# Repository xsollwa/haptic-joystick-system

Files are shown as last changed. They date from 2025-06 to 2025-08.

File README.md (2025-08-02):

# haptic-joystick-system
A handheld controller that uses air pressure to send haptic feedback.

**Created by:** Ruzanna Gaboyan and Philip Golczak

**Date:** June 7, 2025

## Overview

The **Haptic Joystick System** is a *wireless controller that lets you wirelessly control robot arms in XYR directions* using your hand movement and pressure. It includes a two dual axis joystick modules for motion control in XYR directions, and a small squeezable air bulb that sends and receives air pressure signals. The controller *reads how hard you're squeezing using an air pressure sensor and can also send pressure back* into the bulb to communicate resistance.

**Why we made it**: By this project we wanted to make controlling robots more natural by *"feeling what they feel"* in addition to just moving them. This is useful especially in robotics tasks where pressure precision applied by the robot matters: like gripping and squeezing fragile objects. 

//////Note: we removed the screen feature to bring the cost of the project down.

## Features
- **Pneumatic haptic feedback system:** Squeeze a small air bulb to send signals to a robot arm.
- **Joystick control**: Move the robot arm in XYR *(R-Rotation)* directions.
- **Two-way haptic feedback communication:** Air pumping piston mechanism also sends pressure back into the bulb when robot grips something.
- **Wireless communication:** ESP32 hamdles communication between the controller and the robot over Wi-Fi.
- **Custom PCB and 3D case:** Designed and built from scratch for this project.
- **OLED Display:** A little screen shows live data like grip pressure, feedback intensity and other info.
- **Ergonomic handle options:** In addition to the default casing, we CAD-ed an alternate ergonomic grip design for more comfort that can be added on the controller.

Ergonomic handle options: In addition to the default casing, we CAD-modeled an alternate ergonomic grip design for added comfort and modularity when holding the controller.

### Materials and Budget

## Bill of Materials

| Part Number | Part Name | Description | Unit Price | Total Price | Link |
|---|---|---|---|---|---|
| MP1 | ESP32 | Wi-Fi Microprocessor | $5.99 | $5.99 | [Amazon](https://www.amazon.com/gp/product/B0DDPJQX3X/ref=ox_sc_act_image_11?smid=A1VTL661FOEJB1&th=1) |
| J1, J2 | Joystick Module (2x)| KY-023 control joystick module | $6.79 | $6.79 | [Amazon](https://www.amazon.com/Joystick-Sensor-Module-Controller-KY-023/dp/B08681KFSD/) |
| S1 | AITRIP Pressure Sensor | Barometric Pressure Sensor Module | $9.99 | $9.99 | [Amazon](https://www.amazon.com/AITRIP-Pressure-Digital-Barometric-Controller/dp/B09KXXBCYX/) |
| PCB1 | PCB | Fabricated PCB | $5.00 | $5.00 | [PCBWay](https://pcbway.com/) |
| BT1 | Battery Connector | Plug in for LiPo battery | $3.77 | $3.77 | [Amazon](https://www.amazon.com/gp/product/B0DY5GRSQW/ref=ox_sc_act_title_7?smid=AH55IWDCGXER3&psc=1) |
| BULB | Pipet bulb | 4ml Air bulb for pressure sensor | $7.98 | $7.98 | [Amazon](https://www.amazon.com/gp/product/B01LZHMLQA/ref=ox_sc_act_title_6?smid=A29JIFH4ZXPNL8&psc=1) |
| TUBE | Tubes | Tube to connect the sensor, pump and air bulb | $7.49 | $7.49 | [Amazon](https://www.amazon.com/uxcell-Silicone-Tubing-Rubber-Transfer/dp/B085N17TDB/) |
| CN1 | Tube T-Connectors | Connectors for the tube, air bulb, sensor, pump | $11.99 | $11.99 | [Amazon](https://www.amazon.com/gp/product/B06XGCM2RX/ref=ox_sc_act_title_5?smid=A1THAZDOWP300U&psc=1) |
| SYRINGE | Syringe | 10ml Syringe for inflating and deflating | $5.99 | $5.99 | [Amazon](https://www.amazon.com/Plastic-Syringe-Measurement-Scientific-Measuring/dp/B09MYPTD1P/) |
| AT1 | Actuator | Mini Linear Actuator to push air | $19.99 | $19.99 | [Amazon](https://www.amazon.com/Actuator-Electric-Actuators-Robotics-Automation/dp/B0D17H1HGV/) |
| MD1 | Motor Driver | Stepper Motor Driver Module | $6.98 | $6.98 | [Amazon](https://www.amazon.com/WWZMDiB-L298N-H-Bridge-Controller-Raspberry/dp/B0CR6BX5QL/) |
| **TOT** | **Total (excl. taxes & shipping)** | | | **$91.96**  | |
| | **Total WITH taxes & shipping** | | | **$114.50** | |

## Notes on Purchasing and Shipping

We want to purchase most of the parts from Amazon. We chose Amazon as our primary supplier because we have access to Amazon Prime, which has faster shipping. The prime shipping makes the packs cheaper than the singular alternatives at other sources (like AliExpress). Also, we own some of the parts, like the battery and boost converter, so their cost is put as $0. 

//Note: The difference between Aliexpress sourcing and Amazon sourcing for this project is ~$7.00

## How it Works
1) Joystick modules send movement data wirelessly through ESP32 to the robot arm,
2) When you squeeze the air bulb the pressure sensor reads the force,
3) ESP32 sends that signal to the robot (like our [Remote Assist Hand](https://github.com/xsollwa/remote-assist-hand), but the controller can potentially be used on other robots as well),
4) If the robot grips something, it sends resistance signals back,
5) Air pumping mechanism activates and sends pressure into the bulb,
6) You feel it!
7) OLED screen displays pressure data, joystick values, connection status and more. Pressing either joystick down switched between display modes.

## Pictures 
**PCB**

<p align="center">
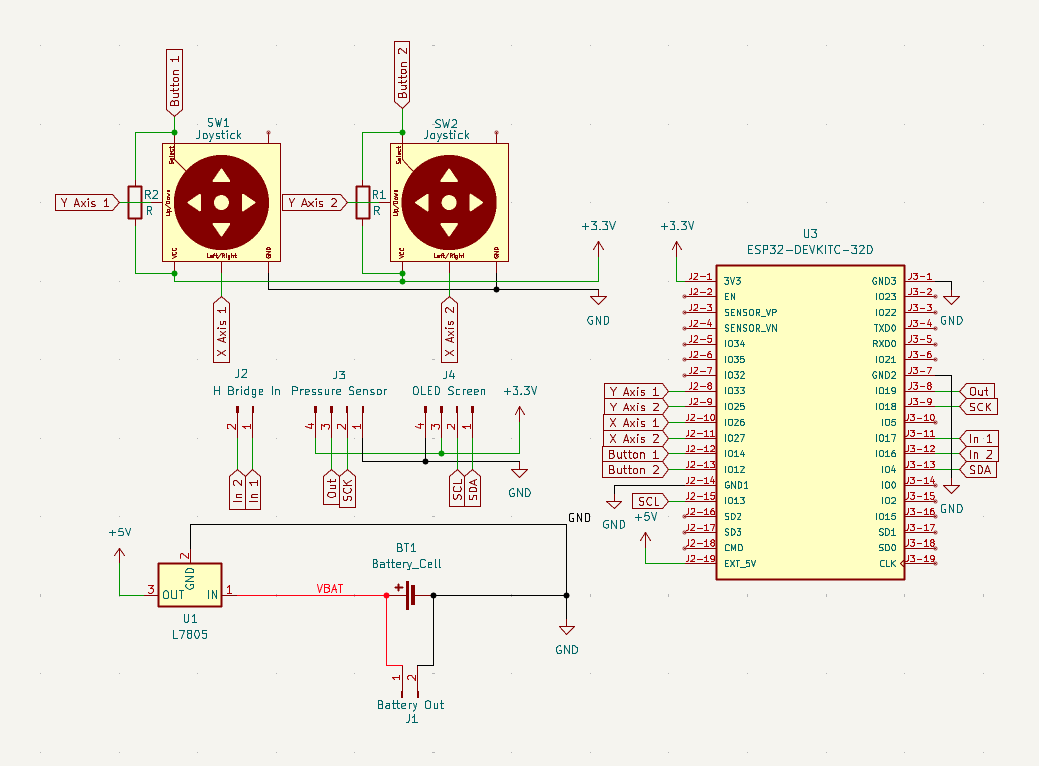
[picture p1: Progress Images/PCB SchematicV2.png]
  
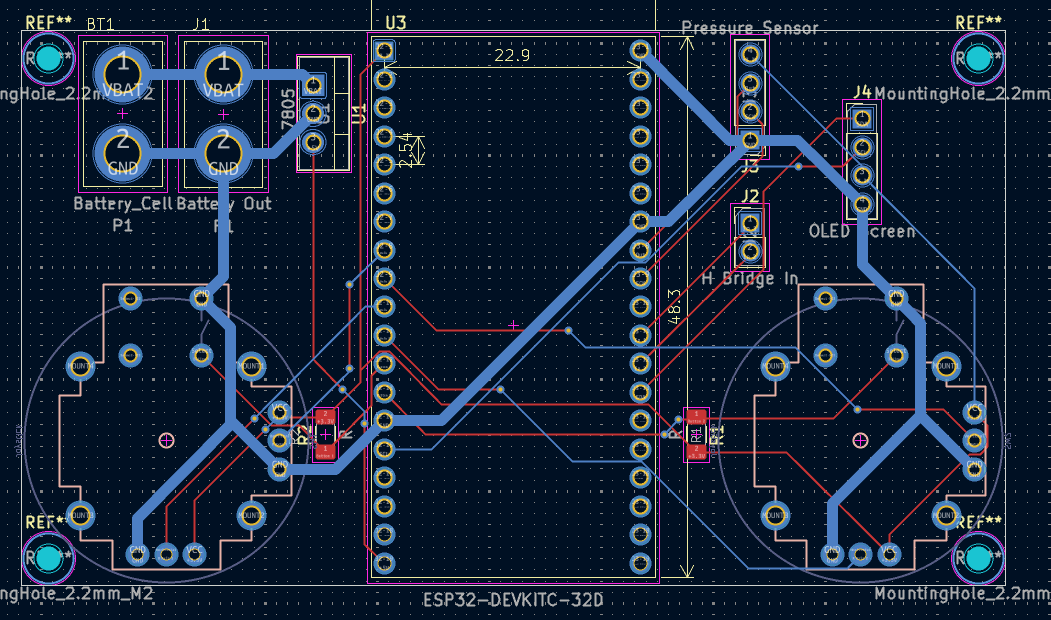
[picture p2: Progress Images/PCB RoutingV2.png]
  
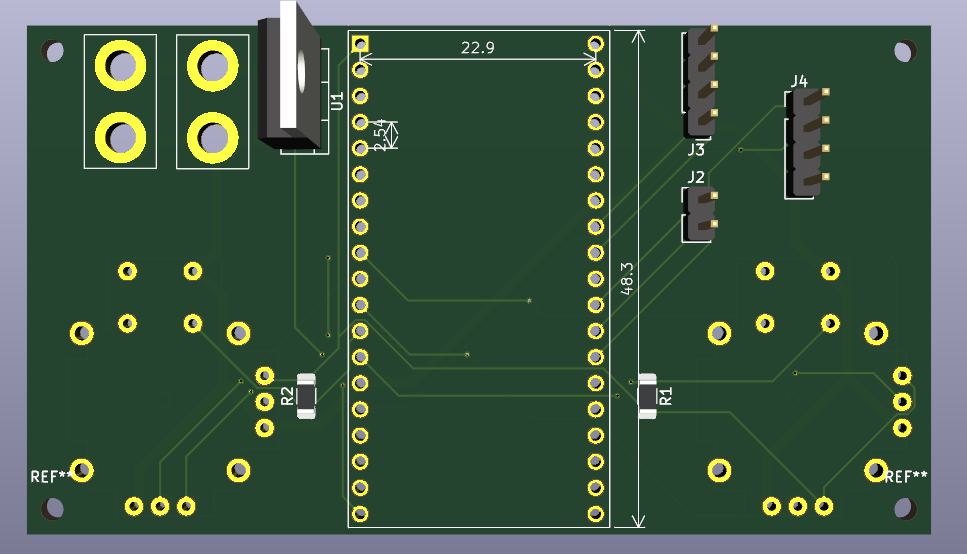
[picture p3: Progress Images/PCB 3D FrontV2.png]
  
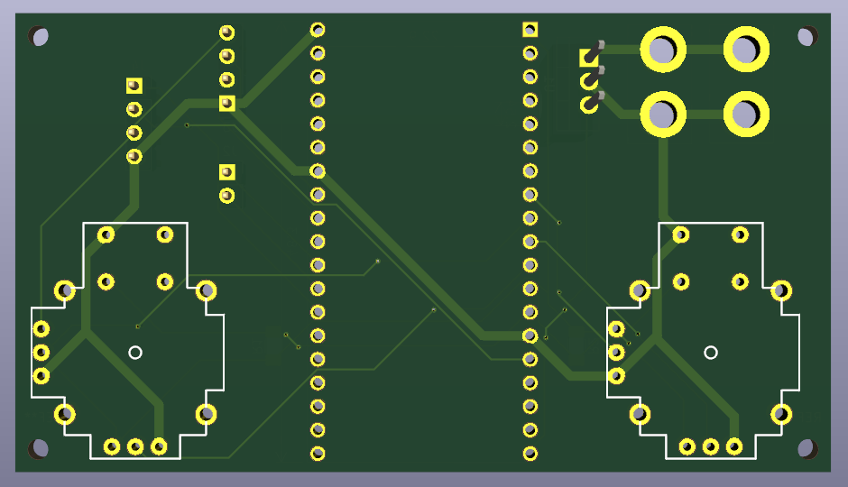
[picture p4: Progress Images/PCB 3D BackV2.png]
  
</p>

**3D model**

<p align="center">
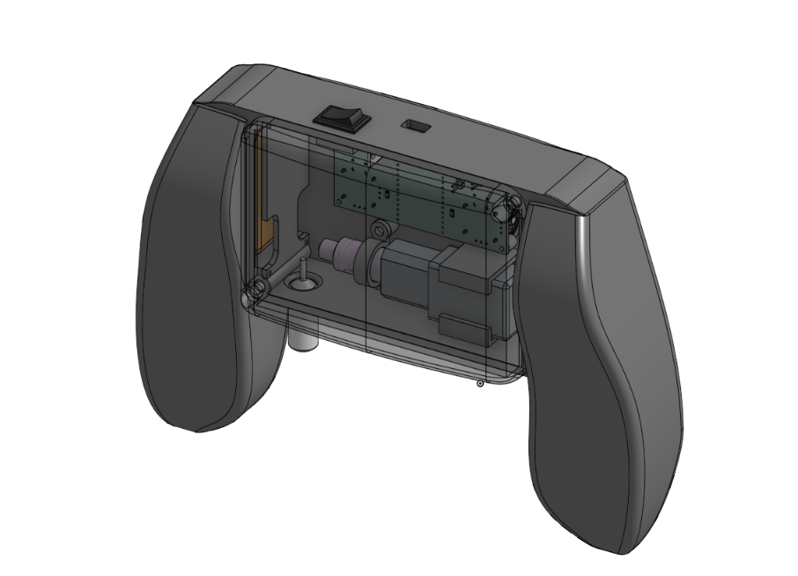
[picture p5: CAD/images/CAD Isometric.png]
Back with Lid
  
  <br>
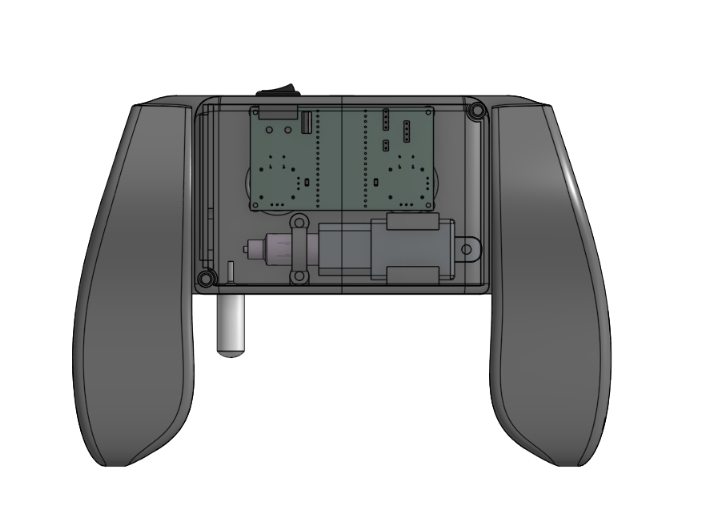
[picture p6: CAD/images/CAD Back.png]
Back
  
  <br>
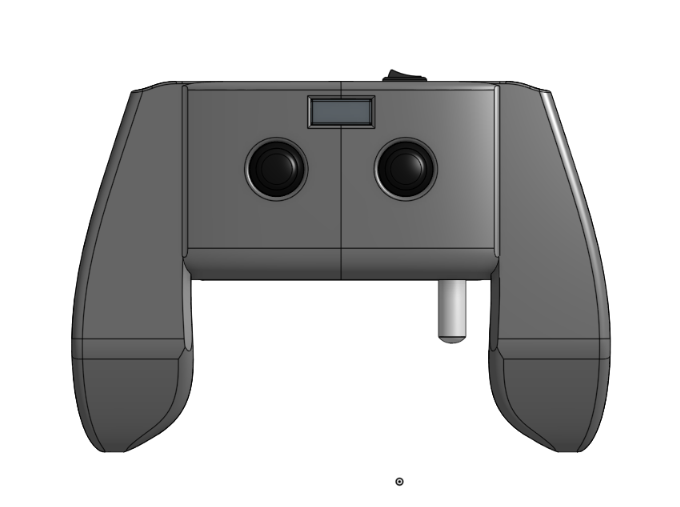
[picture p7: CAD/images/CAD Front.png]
Front
  
</p>

## Building Process
1) Brainstorming and sketches
2) PCB design in KiCAD
3) CAD modeling in OnShape
4) Coding
5) Revision and Optimization
6) Assembly and testing

## Journal
Our full development journal can be found [here](./JOURNAL.md)

## Contact
For any questions or suggestions please reach out to us at *gaboyanruzanna@gmail.com* or *ph.golczak@gmail.com* .

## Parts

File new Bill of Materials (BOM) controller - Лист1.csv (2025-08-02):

Part Number | Part Name | Description | Unit Price | Total Price | Link
MP1 | ESP32 | Wi-Fi Microprocessor | $5.99 | $5.99 | https://www.amazon.com/gp/product/B0DDPJQX3X/ref=ox_sc_act_image_11?smid=A1VTL661FOEJB1&th=1
J1, J2 | Joystick Module (2x) | KY-023 control joystick module | $6.79 | $6.79 | https://www.amazon.com/Joystick-Sensor-Module-Controller-KY-023/dp/B08681KFSD
S1 | AITRIP Pressure Sensor | Barometric Pressure Sensor Module | $9.99 | $9.99 | https://www.amazon.com/AITRIP-Pressure-Digital-Barometric-Controller/dp/B09KXXBCYX?xpid=2-4gjHsH4OvZN
PCB1 | PCB | Fabricated PCB | $5.00 | $5.00 | https://pcbway.com/
BT1 | Battery Connector | Plug in for LiPo battery | $3.77 | $3.77 | https://www.amazon.com/gp/product/B0DY5GRSQW/ref=ox_sc_act_title_7?smid=AH55IWDCGXER3&psc=1
BULB | Pipet bulb | 4ml Air bulb for pressure sensor | $7.98 | $7.98 | https://www.amazon.com/gp/product/B01LZHMLQA/ref=ox_sc_act_title_6?smid=A29JIFH4ZXPNL8&psc=1
TUBE | Tubes | Tube to connect the sensor, pump and air bulb | $7.49 | $7.49 | https://www.amazon.com/uxcell-Silicone-Tubing-Rubber-Transfer/dp/B085N17TDB
CN1 | Tube T-Connectors | Connectors for the tube, air bulb, sensor and pump | $11.99 | $11.99 | https://www.amazon.com/gp/product/B06XGCM2RX/ref=ox_sc_act_title_5?smid=A1THAZDOWP300U&psc=1
SYRINGE | Syringe | 10ml Syringe for inflating and deflating | $5.99 | $5.99 | https://www.amazon.com/Plastic-Syringe-Measurement-Scientific-Measuring/dp/B09MYPTD1P?rnid=2661611011
AT1 | Actuator | Mini Linear Actuator to push air | $19.99 | $19.99 | https://www.amazon.com/Actuator-Electric-Actuators-Robotics-Automation/dp/B0D17H1HGV
MD1 | Motor Driver | Stepper Motor Driver Module | $6.98 | $6.98 | https://www.amazon.com/WWZMDiB-L298N-H-Bridge-Controller-Raspberry/dp/B0CR6BX5QL
TOT | Total (excl. taxes & shipping) |  |  | $91.96
 | Total WITH taxes+shipping |  |  | $114.5

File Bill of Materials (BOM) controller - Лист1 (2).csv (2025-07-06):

Part Number | Part Name | Description | Unit Price | Total Price | Link
MP1 | ESP32 | Wi-Fi Microprocessor | $10 | $10 | https://www.amazon.com/HiLetgo-ESP-WROOM-32-Development-Microcontroller-Integrated/dp/B0718T232Z
B1 | Urgenex Lipo Battery | Battery for the Controller | $27 | $0 (owned) | https://www.amazon.com/URGENEX-Battery-1800mAh-Rechargeable-Campatibal/dp/B0924MM61Z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
BC1 | Buck Converter 4mm (2x) | Buck Converter for 7.4-5v | $8 | $0 (owned) | https://www.amazon.com/Maxmoral-Converter-Adjustable-Step-Down-Regulator/dp/B07MKQXNWG
J1, J2 | Joystick Module (2x) | KY-023 control joystick module | $7 | $7 | https://www.amazon.com/Joystick-Sensor-Module-Controller-KY-023/dp/B08681KFSD
S1 | AITRIP Pressure Sensor | Barometric Pressure Sensor Module | $10 | $10 | https://www.amazon.com/AITRIP-Pressure-Digital-Barometric-Controller/dp/B09KXXBCYX?xpid=2-4gjHsH4OvZN
PCB1 | PCB | Fabricated PCB | $5 | $5 | https://jlcpcb.com/
PINS | Header Pins (20x) | Header Pins to mount joystick/sensor/ESP32 | $9 | $9 | https://www.amazon.com/Female-Header-ESP-WROOM-32-ESP32-DevKitC-Breakout/dp/B0CFDYMRK2
BT1 | Battery Connector | Plug in for LiPo battery | $8 | $8 | https://www.amazon.com/ZHOFONET-Connector-Adapter-Silicone-Battery/dp/B0DCFQPNFS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
BULB | Pipet bulb | 4ml Air bulb for pressure sensor | $23 | $23 | https://www.amazon.com/Globe-Scientific-136020-500-Transfer-Non-Sterile/dp/B00G6T7TK8
TUBE | Tubes | Tube to connect the sensor, pump and air bulb | $8 | $8 | https://www.amazon.com/uxcell-Silicone-Tubing-Rubber-Transfer/dp/B085N17TDB
CN1 | Tube T-Connectors | Connectors for the tube, air bulb, sensor and pump | $6 | $6 | https://www.amazon.com/uxcell-30Pcs-Plastic-Joiner-Connector/dp/B06XFDTLG2
SYRINGE | Syringe | 10ml Syringe for inflating and deflating | $12 | $12 | https://www.amazon.com/Syringe-Without-Liquids-Sterile-Packaged/dp/B0DDH5X9G3
AT1 | Actuator | Mini Linear Actuator to push air | $18 | $18 | https://www.amazon.com/Actuator-Electric-Actuators-Robotics-Automation/dp/B0D17H1HGV
MD1 | Motor Driver | Stepper Motor Driver Module | $7 | $7 | https://www.amazon.com/WWZMDiB-L298N-H-Bridge-Controller-Raspberry/dp/B0CR6BX5QL
SW1 | Boat Rocker Switch | Power Switch | $5 | $5 | https://www.amazon.com/10PCS-Rocker-Switch-Rectangle-Black/dp/B094FWYWL5
TOT | Total (excl. taxes & shipping) |  |  | $128

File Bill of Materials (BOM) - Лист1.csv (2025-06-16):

Part Number | Part Name | Description | Unit Price | Total Price
U3 | ESP32 | Wi-Fi Microprocessor | $10 | $10
BT1 | Urgenex Lipo Battery | Battery for the Controller | $27 | $27
U1 | Buck Converter 4mm (2x) | Buck Converter for 7.4-5v | $8 | $8
R1 | 10k Resistor (100x) | Resistor for voltage divider | $6 | $6
R2 | 15k Resistor (100x) | Resistor for voltage divider | $6 | $6
J2 | ESP32 Joystick Module (2x) | XY control joystick module | $7 | $7
U4 | MPX5010DP sensor | Pressure sensor | $25 | $25
RV1 | Rotary Potentiometer (5x) | Potentiometer for R movement | $10 | $10
J1 | Air Pump | DC mini air/vacuum pump | $8 | $8
Q2 | MOSFET Transistor (10x) | IRLZ44NPBF Logic Level Mosfet | $10 | $10
D1 | Diode (100x) | 1N5819 Schottky Diodes | $3 | $3
PCB | PCB | Fabricated PCB | $5 | $5
HDR | Header Pins (20x) | Header Pins to mount joystick/sensor/ESP32 | $9 | $9
CN1 | Battery Connector | Plug in for LiPo battery | $8 | $8

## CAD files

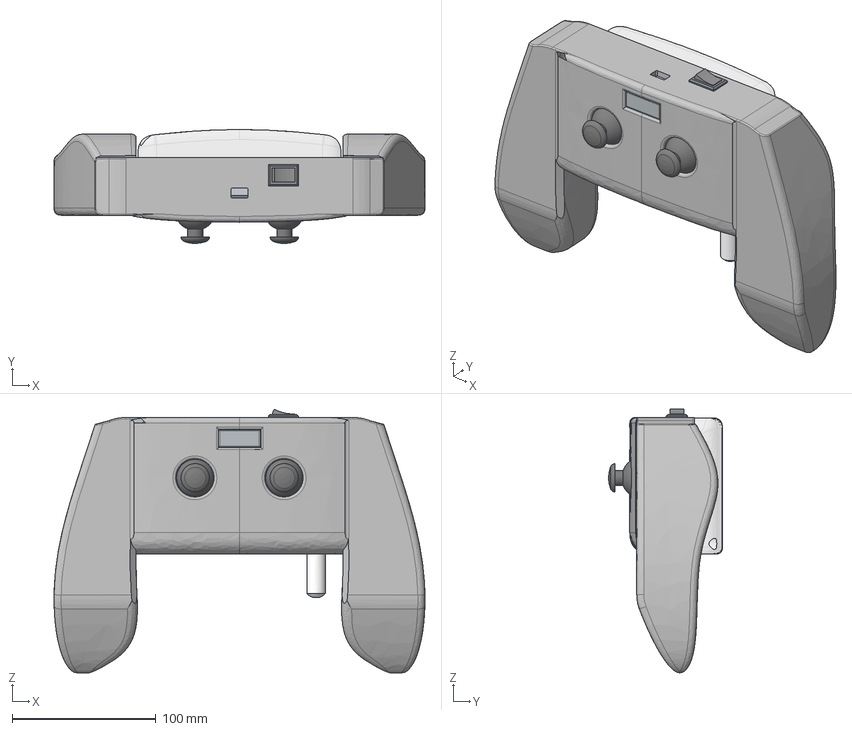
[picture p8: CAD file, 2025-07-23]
CAD/Final Assembly.step
258.3 x 79.4 x 183.5 mm
Tactile-Switch x 2
PinHeader_1x04_P2.54mm_Vertical_1
Case x 2
Potentiometer_02 x 2
Baseplate x 2
TO-220-3_Vertical
Thumb-Button x 2
controllerV2_PCB
PinHeader_1x04_P2.54mm_Vertical
R_1206_3216Metric
PinHeader_1x02_P2.54mm_Vertical
Rotator-Unit x 2
Potentiometer_01 x 2
R_1206_3216Metric_1

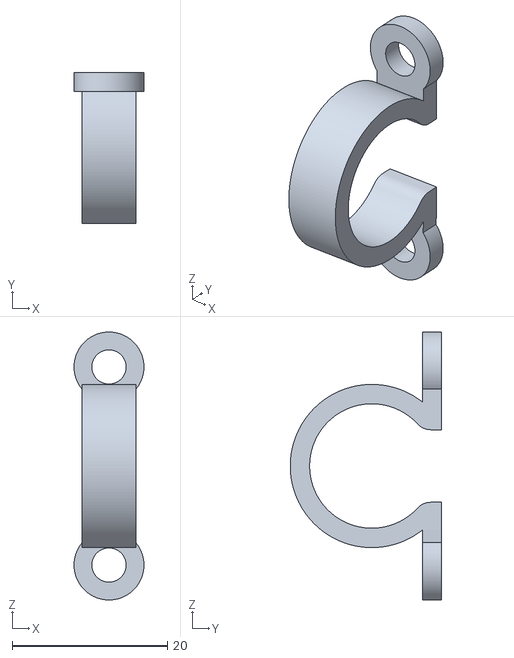
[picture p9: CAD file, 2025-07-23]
Production/STL Files/Syringe Holder (Phil).stl
9.00 x 19.5 x 34.5

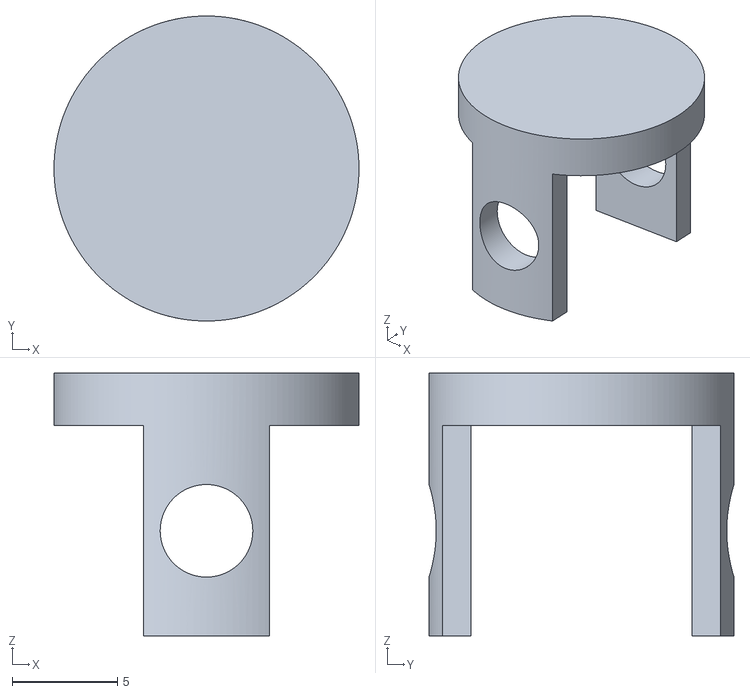
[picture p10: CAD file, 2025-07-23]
Production/STL Files/Syringe Seal Adapter.stl
14.5 x 14.5 x 12.5

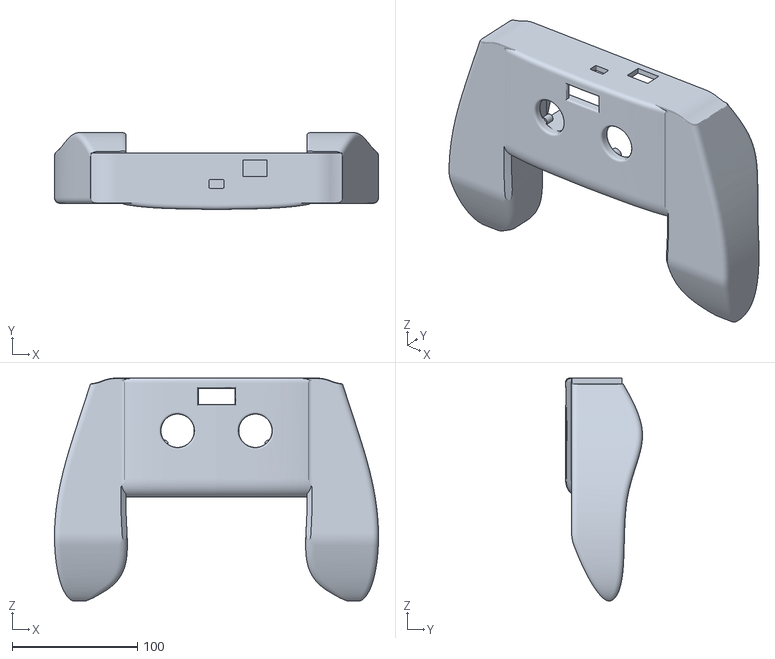
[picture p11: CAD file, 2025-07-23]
Production/STL Files/Front Final.stl
258.3 x 61.4 x 177.8

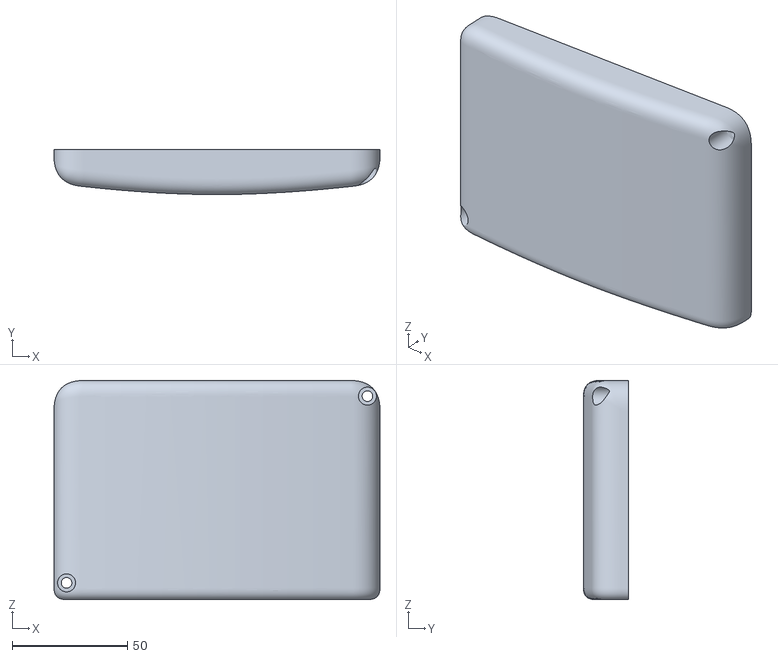
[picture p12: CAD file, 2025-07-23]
Production/STL Files/lid.stl
141.4 x 19.6 x 95.0

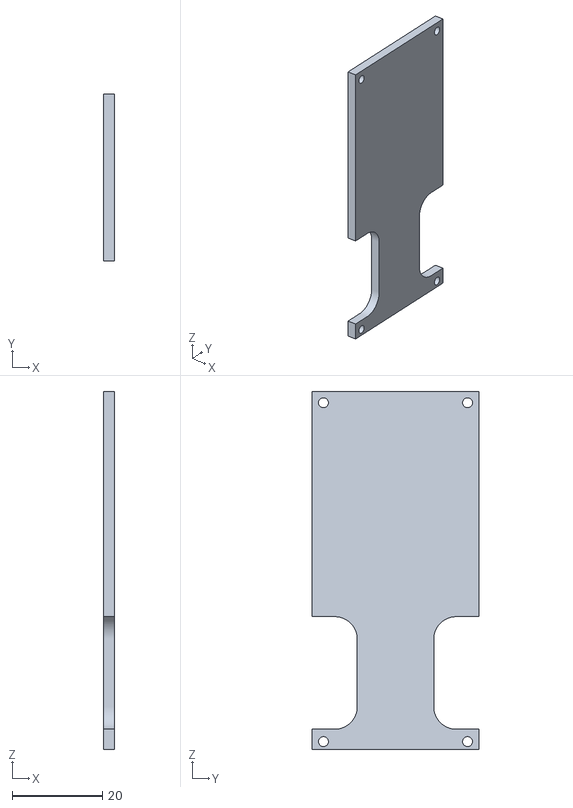
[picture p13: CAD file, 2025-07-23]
Production/STL Files/Battery Holder Final.stl
2.50 x 37.0 x 79.5

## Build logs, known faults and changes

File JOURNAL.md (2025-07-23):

---
Title: "Haptic Joystick System"
Authors: "Ruzanna Gaboyan and Philip Golczak"
Description: "Haptic Joystick System is a controller that uses air pressure to send haptic feedback. It has an air bulb that you squeeze, a tube connected to pressure sensor and joystick-like controls for movement in the X Y and R (rotation) directions."
Created_At: "2025-06-07"
---
# Total time spent (On design): 74 hours
**Ruzanna**: 42 hours

**Philip**: 32 hours

### June 6, 2025 - 2 hours

**What we did:**

- Today we brainstormed ideas for a project that would allow us to incorporate a two-way haptic feedback system and potentially wirelessly interact with robotic builds that have a functional haptic feedback system.
  
- We decided to build a wireless haptic controller that can interact with a robotic arm through pressure-based feedback and multi-axis (XYR) motion input. We will use this controller to control out previous highway project, which is remote haptic feedback hand (check out at https://github.com/xsollwa/remote-assist-hand)
  
- The controller works by letting you control a robot or device using your hand. When you squeeze the air bulb, it sends air to a pressure sensor, which tells the microcontroller how hard you’re squeezing. That information is sent wirelessly to either a robot hand or a balloon that gets bigger or smaller depending on your squeeze. The joystick lets you move the robot left, right, forward, and back, and the knob lets you rotate it.
  
- We also will use a small air pump connected to the bulb to let you feel what the robot is feeling. E.g., if the robot grips something hard, the system pushes air back into your bulb, making it harder to squeeze. This creates two-way feedback because you're not just sending commands buy feeling what’s happening on the other end.
  
### June 7, 2025 - 2 hours

**What we did:**

*Ruzanna*

- Today I created the GitHub repository for this project with its necessary files, and submitted a pull request to Highway project gallery.
  
- Philip and I had a discussion about all materials we would need for this control pad. After having a good idea of how the controller will function I attempted to create the first detailed design sketch of it. This initial sketch would serve as a visual aid to help us conceptualize how the various components will fit and interact within the final assembly. Here is the first sketch with the labeled components!

<p align="center">
  
</p>

After showing the sketch to Philip, we figured that although this control pad would be functional, it would be quite uncomfortable to use. Instead of this design, we decided to incorporate a design that would be fitted to the hand (like an Xbox controller), where the index finger and the thumb of the right hand would pinch the small air bulb, and the left hand would be used for XYR controls. (Also I was missing an air pump in my sketch, which needs to be used in the two-way feedback system)

### June 10, 2025 - 3 hours

**What we did:**

*Ruzanna*

- Following the aforementioned feedback I proceeded to create the 3d design of the controller using OnShape. The holes for the electronics are made considering the sizes of the parts that we found online and planned to obtain.
  Here are some screenshots: (This is my second ever 3d design!)
<p align="center">
  
  
  
</p>

- I sent the 3d design over to Philip for review, revisions and fixing if needed.

### June 11, 2025 - 4 hours

**What we did:**

*Ruzanna*

- Today I created the first schematic for the controller pcb. It was my second time using KiCad after solder so it took A WHILE... but I finally got all the connections in place. I used an ESP32 module as the main microcontroller and wired up a joystick, pressure sensor, potentiometer, and MOSFET-controlled air pump. Getting the voltage regulator set up correctly for the ESP32 was a bit confusing, and figuring out how to wire the MOSFET without frying anything took a few tries. I also added a flyback diode for the air pump to prevent voltage spikes. Laying out all the component symbols and making sure each one had the right number of pins connected was tricky, especially with the ESP32. But by the end, I had a complete schematic I felt pretty good about. Here is a picture of it:



- I sent the schematic to Philip for a double check and some feedback, and it turned out that I was using the wrong ESP32 model and batteries the whole time (I had selected the ESP32-WROOM-32 instead of the correct ESP-WROOM-32, and I was designing around a 4.7V battery instead of the required 7.4V). Philip also also recommended replacing the step-up converter with a buck converter to provide a more stable 5V output for both the microcontroller and the sensor. After reviewing these suggestions, I went back and revised the design. Following the corrections, I created the second (and correct!) version of the schematic:



### June 12, 2025 - 2 hours

**What we did:**

*Ruzanna*

- Today I completed the final PCB layout for the controller. One of the biggest challenges I faced was routing all the connections — with so many components in a compact space, it quickly became difficult to find clean paths for every signal. Eventually, I learnt about vias and used them to complete the pcb!

<p align="center">
  
  
</p>

//nothing super interesting on the back of it

- We also familiarised ourselves with the process of ordering pcbs through PCBWay, since it would be our first time using it.

### June 13, 2025 - 2 hours

**What we did:**

- Today we got the chance to share both of our projects at the Highway Show & Tell with strange parts! It was really interesting and exciting to see all the unique projects made by other hack clubbers, and we certainly learnt a lot from the feedback given by Strange Parts.

*Ruzanna*

- I created the Bill of Materials today, and found all of the parts that we would need to purchace for this project. Everything is written out, including where we will be obtaining the part from in the [MATERIALS-AND-BUDGET.md](MATERIALS-AND-BUDGET.md)

### June 15, 2025 - 1 hour

**What we did**

*Ruzanna*

- Today I completed the README.md file of this project. In the README I covered the overview of the project, its key features, components, work process, build process and included links to important files such as the MATERIALS-AND-BUDGET.md and JOURNAL.md.

## June 17, 2025 - 2 hours

**What we did**

*Ruzanna*

- I uploaded and/or cadded all of the necessary components into my OnShape assembly and put (almost) everything together!


## June 20, 2025 - 3 hours

**What we did**

*Ruzanna* 

- After checking out other joystick designs, I realized my first version would likely be uncomfortable to hold and wouldn’t have enough room for all the components. Because of that, I decided to redesign it from scratch. My updated version has more internal space and an ergonomic shape that better fits the natural contours of the hand, making it much more comfortable to use. So far, I’ve made good progress on version 2 in CAD. It took some time to learn how to use the loft feature properly though.
<p align="center">
  
  
  
</p>

## June 22, 2025 - 4 hours

**What we did**

*Ruzanna*

- I decided to fully redo the controller design again because I wasn’t happy with how it turned out. I thought I could make a cleaner and more comfortable version from scratch. I rounded the overall shape a bit and changed up the handles so they feel better in the hands. I also tried out different layout ideas for the joystick modules and the air bulb to see what would work best. Sketching these out helped me plan the controls and think about how to make everything easier to reach and use. Here are some of my sketches and my third version of the controller!: 
<p align="center">
  
  
</p>
- We also decided to get rid of the potentiometer and use two dual axis joystick modules to be able to percisely control all the motors on the arm.

## June 25, 2025 - 2 hours

- Today I designed the holders for joystick modules and the battery. 
<p align="center">
  
  
</p>

### June 28, 2025 - 3 hours

**What we did**

*Ruzanna*

- Today I mostly focused on designing the controller lid in CAD. I worked on modeling the mounting holes so they would line up with the rest of the assembly, and I also created the cutout for the USB-C port. While working on the lid, I re-mapped the arrangement of all the components inside the cover, since there’s not a lot of space to work with. I tried to place things as efficiently as possible to avoid any interference and to make sure the wiring would stilll be manageable.
  
  

- Later on, we realized that our air pump is not reversible, which would be a problem for creating a functional two-way haptic feedback system. Since we wouldn’t be able to both inflate and deflate the bulb with a non-reversible pump, we started searching for a new reversible air pump. Unfortunately, none of the reversible pumps we found were small enough to fit inside the controller’s limited capacity.

As an alternative, I suggested using a standard air pump along with a valve system. The idea was to switch the pump’s input and output toward the bulb depending on whether we wanted to inflate or deflate it. That’s basically how most balloon inflators and deflators work. But, Philip pointed out that this approach wouldn’t be precise enough for our project, where we need fine control.

Instead, Philip came up with a better mechanism using a syringe moving by a servo motor to move air in and out of the bulb. This design would be a lot more precise while still staying small enough to fit in our controller. After talking it through, we agreed that this was the best way to move forward. Here’s the sketch that Philip made to show the concept:  



- We also figured that our current MXP5010DP sensor does not tolerate pressure above 10kPa, so we decided to switch to Barometric Pressure Sensor Module which can handle up to 40kPa

### June 28, 2025 - 3 hours

**What we did**

*Philip*

- I assisted Ruzanna in brainstorming and creating sketches for possible designs of the controller, specifically considering the use of a motor to push a syringe and precisely control the air pressure within the bulb, as explained above.

### June 29, 2025 - 3 hours

**What we did**

*Ruzanna*

- After coming up with a better mechanism for the controller, which uses a bulb, a syringe, and a servo motor to move the syringe plunger, we started searching for new parts. We found a 4 mL bulb that would fit nicely into the controller, and I ran some calculations to figure out how much air we’d need to inject to reach our maximum target pressure of 50 kPa (about the same as a firm pinch).

- Since the normal air pressure is around 101 kPa (atmospheric), raising the bulb’s pressure to 151 kPa means you’d need to increase the amount of air inside by roughly 50%, so about 50% more air molecules. That comes from the ideal gas law, since pressure and the amount of air are directly proportional in a fixed volume. The bulb’s volume is 4 mL, so at atmospheric pressure it already holds 4 mL worth of air. To get to 151 kPa, you’d inject about 2 mL of air at atmospheric pressure, because the ratio Pressure 2/Pressure 1 equals the ratio of the final to initial air quantity. So we knew we would need a syringe that could move at least 2 mL of air.

Our previous 2 mL bulb wouldn’t have handled that kind of pressure swing without deforming too much, so switching to a 4 mL bulb was the safer option.

<p align="center">
  
</p>

- Next, we went looking for a 2–3 mL syringe small enough to fit inside the controller. Unfortunately, there weren’t any standard syringes in that size range that would physically fit into the space. So we took a 10 mL syringe and decided to cut it down so it could still handle the air volume we needed but stay small enough for the design.

<p align="center">
  
</p>

- Next, we had to figure out how to move the syringe plunger. At first, we planned to use a servo motor, but later Philip found a linear actuator that would be a better alternative because of its uniform horizontal movement and its relatively small size. That should give us more precise control over the air pressure and more consistent haptic feedback.
  
<p align="center">
  
</p>

### June 29, 2025 - 2 hours

**What we did**

*Philip*
- As Ruzanna has detailed above, I assisted in brainstorming and discussing the design of the controller, finding new parts and ideas for how the two-way haptic feedback system will work.

### June 30, 2025 - 2 hours

*Ruzanna*

- Today I imported or designed the parts (new 4ml bulb, new switch, lipo) that we will be using moving forward, and updated the Bill of Materials with the new parts that we found.





### July 2, 2025 - 4 hours

**What we did**

*Ruzanna*
- Today I mainly worked on CAD-ing out the parts (syringe and actuator), casing for electronics and updating the Bill of Materials with the new parts!

Battery casing:




Syringe (and its holder) and actuator:

<p align="center">
  
  
  
  
</p>

### July 2, 2025 - 7 hours

**What we did**

*Philip*
- Today, I worked on remaking the PCB that Ruzanna had previously worked on, since the planes for the controller had changed a lot recently. Many of the parts we had to include also changed. I also had to update some of the footprints she was using since I had mistakenly given her the wrong ones. Using her previous PCB design as a reference, I remade it, making it more compact and changing the components to suit our needs. Below are images of the new PCB.
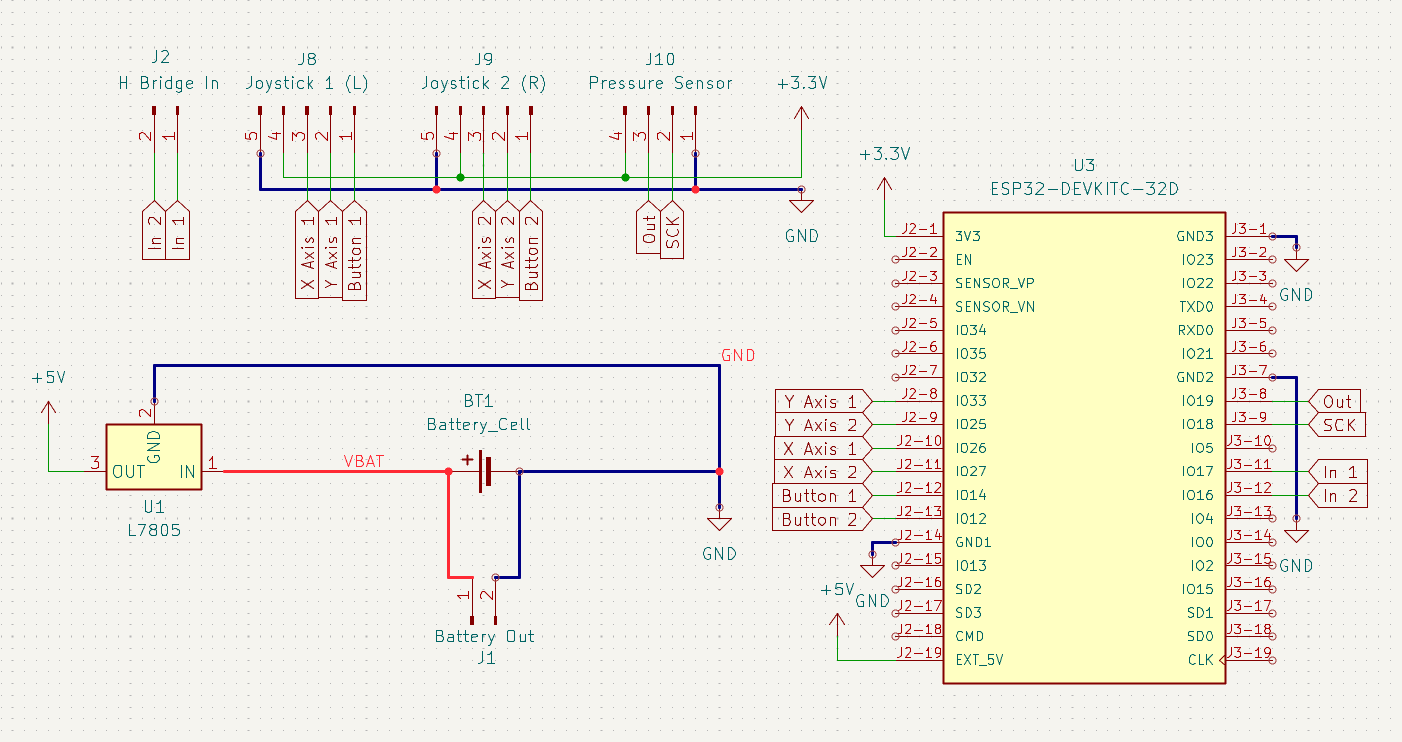
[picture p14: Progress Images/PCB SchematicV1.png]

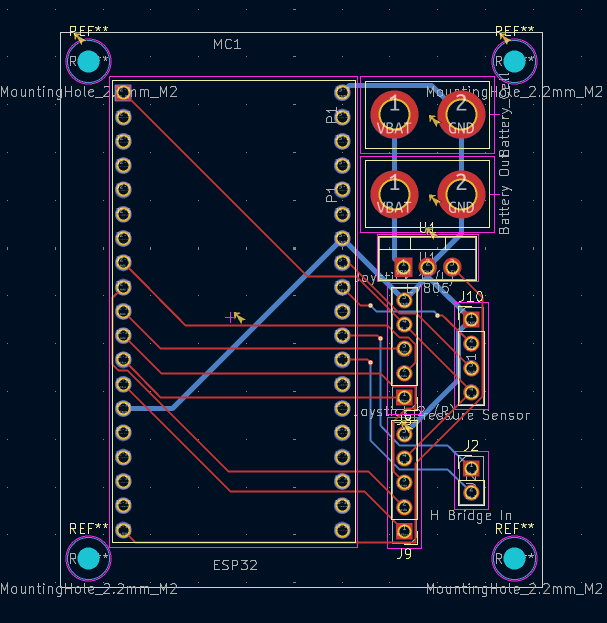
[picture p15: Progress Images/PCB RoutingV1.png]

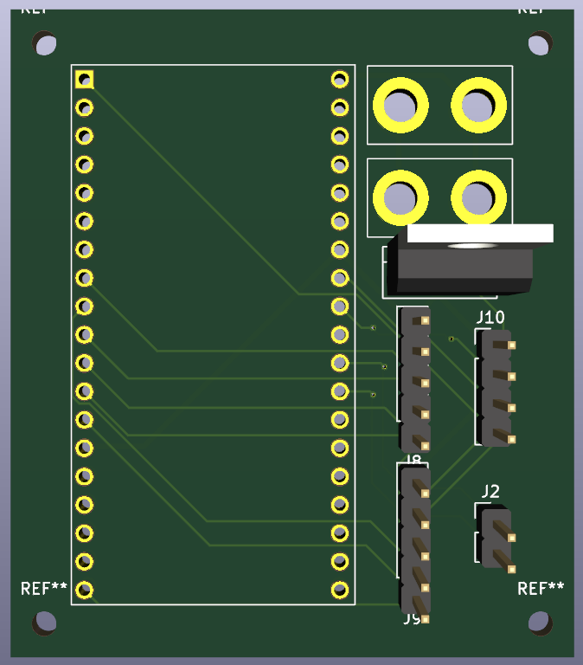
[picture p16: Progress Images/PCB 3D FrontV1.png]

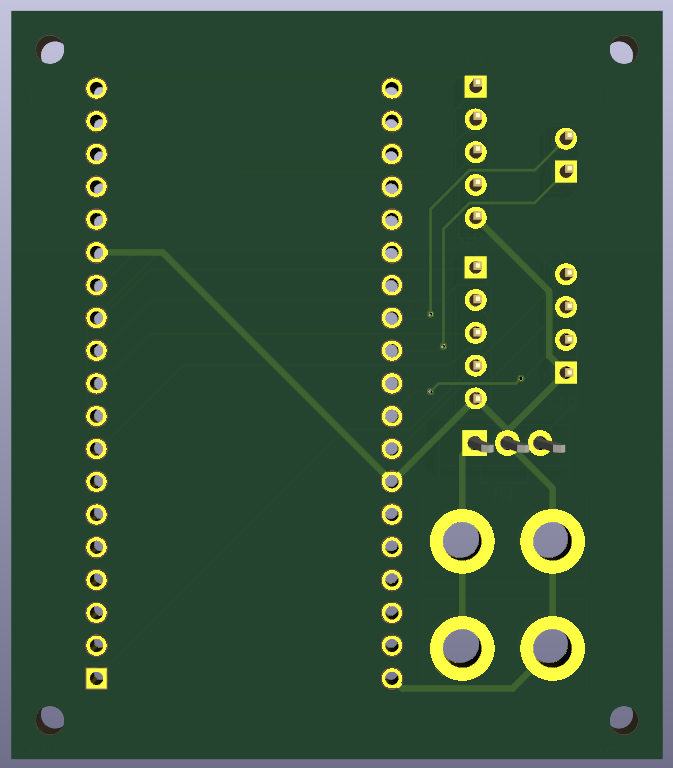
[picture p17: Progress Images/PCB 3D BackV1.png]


### July 3, 2025 - 6 hours

**What we did**

*Philip*
- Today, I created the code for the ESP32 controller and modified the code from our ARM project so that it can be controlled not only through the webpage but also through the controller, allowing for a proper two-way closed haptic feedback system. This system will work by the ESP32 in the arm sending amplified signals from the load cell in the grasper, giving pressure feedback. In the controller there will be a 4mL pipet bulb which the user will squeeze which is hooked up to both a pressure sensor as well as a syrige filled with air and a linear actuator which will increase the pressure in the bulb to a maximum of 40 kPa (the equivalent of a tight pinch) as the load cell expereinces more and more force. However, as the pressure rises from the user squeezing the bulb, so will the force on the load cell as the grasper squeezes tighter.

### July 4, 2025 - 5 hours

**What we did**

*Philip*
- Today, I worked on refining the CAD and preparing it for printing, adding the plunger adapter part for the linear actuator, and making adjustments to tolerances. I also ensured that all threaded inserts and screws would fit well into the design. Below are some images of the adapter and the completed CAD.
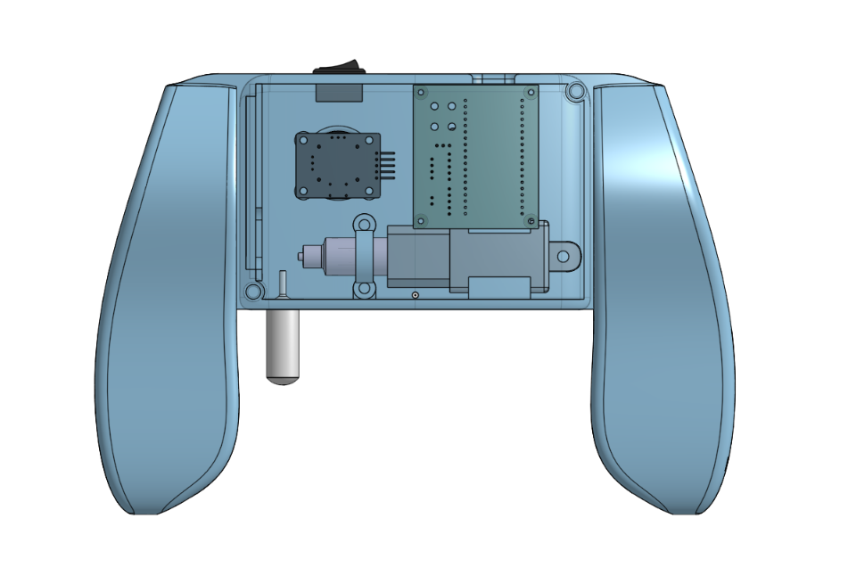
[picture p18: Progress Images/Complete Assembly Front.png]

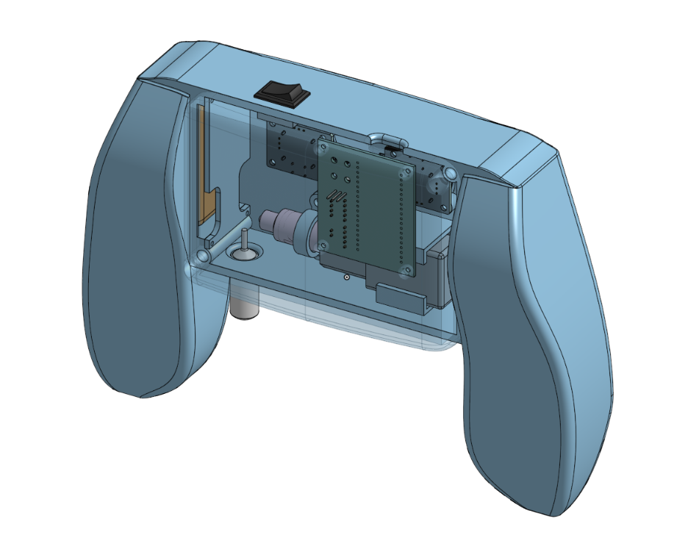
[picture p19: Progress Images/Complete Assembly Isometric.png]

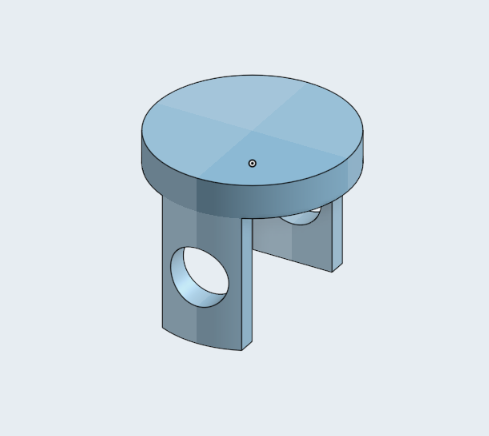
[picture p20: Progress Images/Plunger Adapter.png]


### July 6, 2025 - 3 hours

**What we did**

*Ruzanna*
- Today I organized the repository, made the final changes in readme, BOM, the journal and other files, making sure everything meets the submission requirements.

### July 10, 2025 - 1 hour

**What we did**

*Ruzanna*
- I made some changes in the code to improve how the joystick data is handled. I made the joystick center values calibrate automatically instead of using a fixed number. This helps the robot move more based on the real joystick position. I also added Wi-Fi and WebSocket reconnect logic so the it can recover if the connection drops.

### July 18, 2025 - 2 hours

**What we did**

*Ruzanna*
- To make this controller more advanced, Philip and I decided to utilize all of the buttons on our joystick modules and add a little display. It’s one of those tiny 128x32 displays, and I got it coded with the Adafruit library. I set it up to show four different screens that I will be able to flip through by clicking down on the joystick buttons.

The pages show:
- Arm force (from the robot’s grasper)
- My bulb pressure (from the HX711)
- Live joystick values (to check how it’s reading my input)
- And a little status screen with Wi-Fi info and whether the WebSocket is connected



### July 19, 2025 - 5 hours

**What we did**

*Philip*
- Today, I focused all my efforts on putting the finishing touches on the project while striving to make it advanced. Specifically, I worked primarily on the PCB, integrating the joystick modules into our custom PCB and adding connectors for the OLED screen. Additionally, I ensured the PCB was well-equipped to handle the high power from the LIPO battery by utilizing KiCAD's netclasses and making certain vital power connections thicker to support the high voltage and current. Additionally, I refined the CAD design, modifying the mounting position for the PCB to accommodate the embedded joystick modules, as well as relocating the programming port. Overall the design for the controller is quite advanted with the two way closed pressure feedback system which requires precision controlls and calibration, its power scheme from a lipo batter being used not only to power the microcontroller, sensor, joysticks, and screen through a 5v regulator but also powering the linear actuator directly, lastly with this precision custom PCB I am very proud of this project. Below are pictures of the updates I have made.






Back with Lid
Back
Front

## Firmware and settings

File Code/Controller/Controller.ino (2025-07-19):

#include <WiFi.h>
#include <WebSocketsClient.h>
#include <ArduinoJson.h>
#include <HX711.h>
#include <Wire.h>
#include <Adafruit_GFX.h>
#include <Adafruit_SSD1306.h>

// Wi-Fi & Ws client
const char* WIFI_SSID = "YOUR_SSID";
const char* WIFI_PWD  = "YOUR_PASSWORD";
WebSocketsClient ws;
const char* ARM_HOST  = "arm.local";
const uint16_t ARM_PORT = 81;
const char* ARM_PATH  = "/ws";

// Joysticks
const int J1X = 34, J1Y = 35, J2X = 32, J2Y = 33;
const int J1_BTN = 23, J2_BTN = 22;
const int BUF_LEN = 5, SAMPLE_MS = 10;
int buf1x[BUF_LEN] = {}, buf1y[BUF_LEN] = {}, buf2x[BUF_LEN] = {}, buf2y[BUF_LEN] = {};
int bufIdx = 0;
int ctr1x = 2048, ctr1y = 2048, ctr2x = 2048, ctr2y = 2048;  // Midpoints
const float ADC_MAX = 2048.0;
volatile float lastArmForce = 0;
const int DEADZONE_PCT = 5;
int DEADZONE = ADC_MAX * DEADZONE_PCT / 100;

// HX711 for bulb pressure
const int BULB_DT = 19, BULB_SCK = 18;
HX711 bulbScale;

// H-bridge pins for actuator
const int H1 = 17, H2 = 16;

// OLED 
#define SCREEN_WIDTH 128
#define SCREEN_HEIGHT 32
Adafruit_SSD1306 display(SCREEN_WIDTH, SCREEN_HEIGHT, &Wire, -1);
int screenPage = 0;
const int NUM_PAGES = 4;

// WS reconnect flag
bool wsReconnectNeeded = false;

// Moving average filter
float avgFilter(int raw, int* buf) {
  buf[bufIdx] = raw;
  long sum = 0;
  for (int i = 0; i < BUF_LEN; i++) sum += buf[i];
  return float(sum) / BUF_LEN;
}

// WS events
void onWsEvent(WStype_t type, uint8_t* data, size_t len) {
  if (type == WStype_DISCONNECTED) {
    Serial.println("WebSocket disconnected, reconnecting...");
    wsReconnectNeeded = true;
  } else if (type == WStype_CONNECTED) {
    Serial.println("WS to arm OK");
  } else if (type == WStype_TEXT) {
    StaticJsonDocument<128> doc;
    if (!deserializeJson(doc, data, len) &&
        String(doc["type"]) == "force" &&
        String(doc["motor"]) == "grasper_servo") {
      lastArmForce = doc["force"].as<float>();
    }
  }
}

void calibrateJoysticks() {
  ctr1x = analogRead(J1X);
  ctr1y = analogRead(J1Y);
  ctr2x = analogRead(J2X);
  ctr2y = analogRead(J2Y);
  Serial.printf("Joystick centers calibrated: J1(%d,%d), J2(%d,%d)\n", ctr1x, ctr1y, ctr2x, ctr2y);
}

void updateDisplay(float j1x, float j1y, float j2x, float j2y, float kPa) {
  display.clearDisplay();
  display.setTextColor(SSD1306_WHITE);
  display.setCursor(0, 0);
  switch (screenPage) {
    case 0:
      display.setTextSize(1);
      display.println("Arm Force:");
      display.setTextSize(2);
      display.print(lastArmForce, 2); display.println(" N");
      break;
    case 1:
      display.setTextSize(1);
      display.println("Bulb Pressure:");
      display.setTextSize(2);
      display.print(kPa, 2); display.println(" kPa");
      break;
    case 2:
      display.setTextSize(1);
      display.println("Joystick Values:");
      display.printf("J1 X: %.2f\n", j1x);
      display.printf("J1 Y: %.2f\n", j1y);
      display.printf("J2 X: %.2f\n", j2x);
      display.printf("J2 Y: %.2f\n", j2y);
      break;
    case 3:
      display.setTextSize(1);
      display.print("SSID: "); display.println(WiFi.SSID());
      display.print("IP: "); display.println(WiFi.localIP());
      display.print("WS: "); display.println(ws.isConnected() ? "Connected" : "Lost");
      break;
  }
  display.display();
}

void setup() {
  Serial.begin(115200);
  analogReadResolution(12);

  pinMode(J1_BTN, INPUT_PULLUP);
  pinMode(J2_BTN, INPUT_PULLUP);

  // H-bridge setup
  pinMode(H1, OUTPUT); pinMode(H2, OUTPUT);
  digitalWrite(H1, LOW); digitalWrite(H2, LOW);

   if (!display.begin(SSD1306_SWITCHCAPVCC, 0x3C)) {
    Serial.println("SSD1306 allocation failed");
    while (1);
  }

  // HX711 setup
  bulbScale.begin(BULB_DT, BULB_SCK);
  bulbScale.set_scale(1.0); 
  bulbScale.tare();

  // Wi-Fi connect
  WiFi.begin(WIFI_SSID, WIFI_PWD);
  Serial.print("Connecting to Wi-Fi");
  while (WiFi.status() != WL_CONNECTED) {
    delay(300); Serial.print('.');
  }
  Serial.println(" connected");

  // Calibrate joystick 
  calibrateJoysticks();
  ws.begin(ARM_HOST, ARM_PORT, ARM_PATH);
  ws.onEvent(onWsEvent);
}

void loop() {

  static bool j1Prev = HIGH, j2Prev = HIGH;
  bool j1Now = digitalRead(J1_BTN);
  bool j2Now = digitalRead(J2_BTN);
  if (j1Prev == HIGH && j1Now == LOW) screenPage = (screenPage + 1) % NUM_PAGES;
  if (j2Prev == HIGH && j2Now == LOW) screenPage = (screenPage - 1 + NUM_PAGES) % NUM_PAGES;
  j1Prev = j1Now;
  j2Prev = j2Now;

  // Reconnect Wi-Fi 
  if (WiFi.status() != WL_CONNECTED) {
    Serial.println("Wi-Fi lost, reconnecting...");
    WiFi.begin(WIFI_SSID, WIFI_PWD);
    delay(500);
    return;
  }

  // Reconnect WebSocket 
  if (wsReconnectNeeded) {
    wsReconnectNeeded = false;
    ws.begin(ARM_HOST, ARM_PORT, ARM_PATH);
    ws.onEvent(onWsEvent);
  }

  ws.loop();

  static unsigned long last = millis();
  if (millis() - last < SAMPLE_MS) return;
  last = millis();

  // read joysticks
  int r1x = analogRead(J1X) - ctr1x;
  int r1y = analogRead(J1Y) - ctr1y;
  int r2x = analogRead(J2X) - ctr2x;
  int r2y = analogRead(J2Y) - ctr2y;

  r1x = abs(r1x) < DEADZONE ? 0 : r1x;
  r1y = abs(r1y) < DEADZONE ? 0 : r1y;
  r2x = abs(r2x) < DEADZONE ? 0 : r2x;
  r2y = abs(r2y) < DEADZONE ? 0 : r2y;

  float j1x = avgFilter(r1x, buf1x) / ADC_MAX;
  float j1y = avgFilter(r1y, buf1y) / ADC_MAX;
  float j2x = avgFilter(r2x, buf2x) / ADC_MAX;
  float j2y = avgFilter(r2y, buf2y) / ADC_MAX;
  bufIdx = (bufIdx + 1) % BUF_LEN;

  // send joystick JSON
  StaticJsonDocument<128> jd;
  jd["type"] = "joystick";
  jd["j1x"] = j1x;
  jd["j1y"] = j1y;
  jd["j2x"] = j2x;
  jd["j2y"] = j2y;
  String out;
  serializeJson(jd, out);
  ws.sendTXT(out);

  // read & send pressure data
  float raw = bulbScale.get_units(5);
  float kPa = raw * 1.0; // Replace with calibrated multiplier
  StaticJsonDocument<128> fd;
  fd["type"] = "force";
  fd["motor"] = "grasper_servo";
  fd["force"] = kPa;
  String fo;
  serializeJson(fd, fo);
  ws.sendTXT(fo);

  // match arm’s force via H-bridge
   float err = lastArmForce - kPa;
  if (err > 1.0) {
    digitalWrite(H1, HIGH); digitalWrite(H2, LOW);
  } else if (err < -1.0) {
    digitalWrite(H1, LOW); digitalWrite(H2, HIGH);
  } else {
    digitalWrite(H1, LOW); digitalWrite(H2, LOW);
  }

  updateDisplay(j1x, j1y, j2x, j2y, kPa);
}

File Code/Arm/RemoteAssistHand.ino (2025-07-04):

#include <WiFi.h>
#include <WebServer.h>
#include <WebSocketsServer.h>
#include <ArduinoJson.h>
#include <AccelStepper.h>
#include <ESP32Servo.h>
#include "HX711.h"
#include "main_page.h"

// Wi-Fi credentials
const char* ssid     = "YOUR_SSID";
const char* password = "YOUR_PASSWORD";

// HTTP + WebSocket servers
WebServer        httpServer(80);
WebSocketsServer webSocket(81);

// Arm’s load cell (HX711)
#define ARM_DT  18
#define ARM_SCK 19
HX711 armScale;

// Motor pins
#define STEP_PIN 14
#define DIR_PIN  27
#define RST_PIN  12

#define SHOULDER_PIN 32
#define ELBOW_PIN    33
#define WRIST_PIN    25
#define GRASPER_PIN  26

// Motion & force settings
const float STEPPER_MAX_SPEED    = 800.0;
const float STEPPER_ACCELERATION = 400.0;
const float SERVO_STEP_DEG       =   2.0;
const float SERVO_MAX_ANGLE      = 270.0;
const float ARM_CAL              =   1.0;  // N per raw unit
const unsigned long FORCE_INTERVAL = 200;

// State & objects
AccelStepper baseStepper(AccelStepper::DRIVER, STEP_PIN, DIR_PIN);
Servo       shoulder, elbow, wrist, grasper;
unsigned long lastForceTime = 0;

// For controller-mode
bool discreteMode = true;
float joy1x=0, joy1y=0, joy2x=0, joy2y=0;
float remoteForce = 0;

// Servo angles
float shoulderAngle = SERVO_MAX_ANGLE/2,
      elbowAngle    = SERVO_MAX_ANGLE/2,
      wristAngle    = SERVO_MAX_ANGLE/2,
      grasperAngle  = SERVO_MAX_ANGLE/2;

// Forward prototypes
void handleWs(uint8_t, WStype_t, uint8_t*, size_t);
void broadcastForce();

void setup() {
  Serial.begin(115200);
  // Stepper reset
  pinMode(RST_PIN, OUTPUT);
  digitalWrite(RST_PIN, HIGH);
  baseStepper.setMaxSpeed(STEPPER_MAX_SPEED);
  baseStepper.setAcceleration(STEPPER_ACCELERATION);
  // Servos
  shoulder.attach(SHOULDER_PIN, 500, 2500);
  elbow   .attach(ELBOW_PIN,    500, 2500);
  wrist   .attach(WRIST_PIN,    500, 2500);
  grasper .attach(GRASPER_PIN,  500, 2500);
  // Center servos
  for (Servo* s: {&shoulder,&elbow,&wrist,&grasper}) {
    s->writeMicroseconds(map(int(SERVO_MAX_ANGLE/2),0,int(SERVO_MAX_ANGLE),500,2500));
  }
  // HX711
  armScale.begin(ARM_DT, ARM_SCK);
  armScale.set_scale(1.0);
  armScale.tare();
  // Wi-Fi
  WiFi.begin(ssid,password);
  Serial.print("WiFi ");
  while (WiFi.status()!=WL_CONNECTED) { delay(300); Serial.print('.'); }
  Serial.println(" OK");
  // HTTP UI
  httpServer.on("/", HTTP_GET, [](){
    httpServer.send_P(200,"text/html",MAIN_PAGE);
  });
  httpServer.begin();
  // WebSocket
  webSocket.begin();
  webSocket.onEvent(handleWs);
}

void loop() {
  httpServer.handleClient();
  webSocket.loop();
  if (discreteMode) {
    baseStepper.run();
  } else {
    baseStepper.setSpeed(joy1x * STEPPER_MAX_SPEED);
    baseStepper.run();
    shoulderAngle = constrain(shoulderAngle + joy1y*SERVO_STEP_DEG, 0, SERVO_MAX_ANGLE);
    elbowAngle    = constrain(elbowAngle    + joy2y*SERVO_STEP_DEG, 0, SERVO_MAX_ANGLE);
    wristAngle    = constrain(wristAngle    + joy2x*SERVO_STEP_DEG, 0, SERVO_MAX_ANGLE);
    shoulder.writeMicroseconds(map(int(shoulderAngle),0,int(SERVO_MAX_ANGLE),500,2500));
    elbow   .writeMicroseconds(map(int(elbowAngle),   0,int(SERVO_MAX_ANGLE),500,2500));
    wrist   .writeMicroseconds(map(int(wristAngle),   0,int(SERVO_MAX_ANGLE),500,2500));
  }
  // Grasper from remoteForce
  grasperAngle = constrain(remoteForce/40.0 * SERVO_MAX_ANGLE, 0, SERVO_MAX_ANGLE);
  grasper.writeMicroseconds(map(int(grasperAngle),0,int(SERVO_MAX_ANGLE),500,2500));
  // Broadcast own force
  if (millis() - lastForceTime >= FORCE_INTERVAL) {
    lastForceTime = millis();
    float raw = armScale.get_units(5);
    float fn  = raw * ARM_CAL;
    StaticJsonDocument<128> d;
    d["type"]="force"; d["motor"]="grasper_servo"; d["force"]=fn;
    String o; serializeJson(d,o);
    webSocket.broadcastTXT(o);
  }
}

void handleWs(uint8_t num, WStype_t type, uint8_t* p, size_t len) {
  if (type!=WStype_TEXT) return;
  StaticJsonDocument<256> d;
  if (deserializeJson(d,p,len)) return;
  String t = d["type"];
  if (t=="move") {
    discreteMode=true;
    String m=d["motor"], dir=d["dir"];
    if (m=="base_stepper") {
      baseStepper.setSpeed(dir=="cw"?STEPPER_MAX_SPEED:-STEPPER_MAX_SPEED);
    } else {
      Servo* sv; float* ang;
      if      (m=="shoulder_servo"){sv=&shoulder;ang=&shoulderAngle;}
      else if (m=="elbow_servo")   {sv=&elbow;   ang=&elbowAngle;}
      else if (m=="wrist_servo")   {sv=&wrist;   ang=&wristAngle;}
      else if (m=="grasper_servo") {sv=&grasper; ang=&grasperAngle;}
      *ang = constrain(*ang + (dir=="cw"?SERVO_STEP_DEG:-SERVO_STEP_DEG),
                      0, SERVO_MAX_ANGLE);
      sv->writeMicroseconds(map(int(*ang),0,int(SERVO_MAX_ANGLE),500,2500));
    }
  }
  else if (t=="stop" && String(d["motor"])=="base_stepper") {
    baseStepper.setSpeed(0);
  }
  else if (t=="joystick") {
    discreteMode=false;
    joy1x=d["j1x"].as<float>();
    joy1y=d["j1y"].as<float>();
    joy2x=d["j2x"].as<float>();
    joy2y=d["j2y"].as<float>();
  }
  else if (t=="force" && String(d["motor"])=="grasper_servo") {
    remoteForce = d["force"].as<float>();
  }
}

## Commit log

2025-06-07 Create MATERIALS-AND-BUDGET
2025-06-13 Update MATERIALS-AND-BUDGET
2025-06-16 Update and rename Bill of Materials (BOM) - Лист1.csv to Bill of Materials (BOM).csv
    [Bill of Materials (BOM).csv]
2025-06-16 Update and rename Bill of Materials (BOM) - Лист1 (1).csv to Bill of Materials (BOM).csv
    [Bill of Materials (BOM).csv]
2025-06-16 Rename Screenshot 2025-06-13 144023.png to pcb.png
2025-06-16 Rename Screenshot 2025-06-13 144101.png to schematic.png
2025-07-03 Update and rename Bill of Materials (BOM) controller - Лист1.csv to Bill of Materials (BOM).csv
    [Bill of Materials (BOM).csv]
2025-07-06 Rename Controller Assembly.step to CAD/Controller Assembly.step
    [Controller Assembly.step]
2025-07-06 Rename CAD/Screenshot 2025-07-05 223224.png to CAD/images/back.png
2025-07-06 Rename Controller Lid.step to Production/Controller Lid.step
    [Controller Lid.step]
2025-07-06 Updated PCB and Production Folders (July 6)
    [Controller Assembly.step, Controller Battery Holder.step, Controller Front.step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]
2025-07-06 Update Bill of Materials (BOM).csv
    [Bill of Materials (BOM).csv]
2025-07-06 Update and rename Bill of Materials (BOM) controller - Лист1 (2).csv to Bill of Materials (BOM)
2025-07-06 Update and rename Bill of Materials (BOM) to Bill of Materials (BOM).csv
    [Bill of Materials (BOM).csv]
2025-07-19 add oled screen + screen switching using joystick buttons
2025-07-23 Updated PCB and CAD (July 22)
    [Battery Holder Final.stl, Controller Assembly.step, Controller Battery Holder.step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]
2025-07-24 Updated BOM.csv (July 24)
    [Bill of Materials (BOM).csv]
